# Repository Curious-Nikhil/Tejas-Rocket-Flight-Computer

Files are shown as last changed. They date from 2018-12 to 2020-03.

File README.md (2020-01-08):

# Tejas Flight Computer
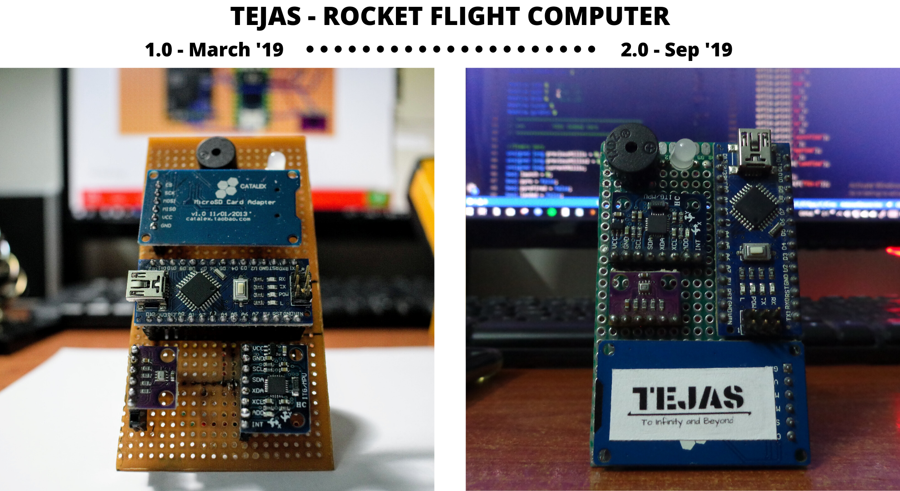
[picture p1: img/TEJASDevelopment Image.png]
TEJAS FC Development

# Software Design

> I prefer to sail in a bad ship with a good captain rather than sail in good ship with a bad captain.

TEJAS flight computer is to aid a model rocket with recovery and data logging. It is entirely based on arduino with MPU6050 and BMP280 for orientation and altitude data. The development of TEJAS FC took over 3 months. It was fundamentally designed with no blocking code so as to make it a fault taularent system to some degree.

## Challenges:
-   
-   Low memory
-   Less Processing Power
-   Delayed Apogge Detection
-   Realtime telemetry

## Flowchart
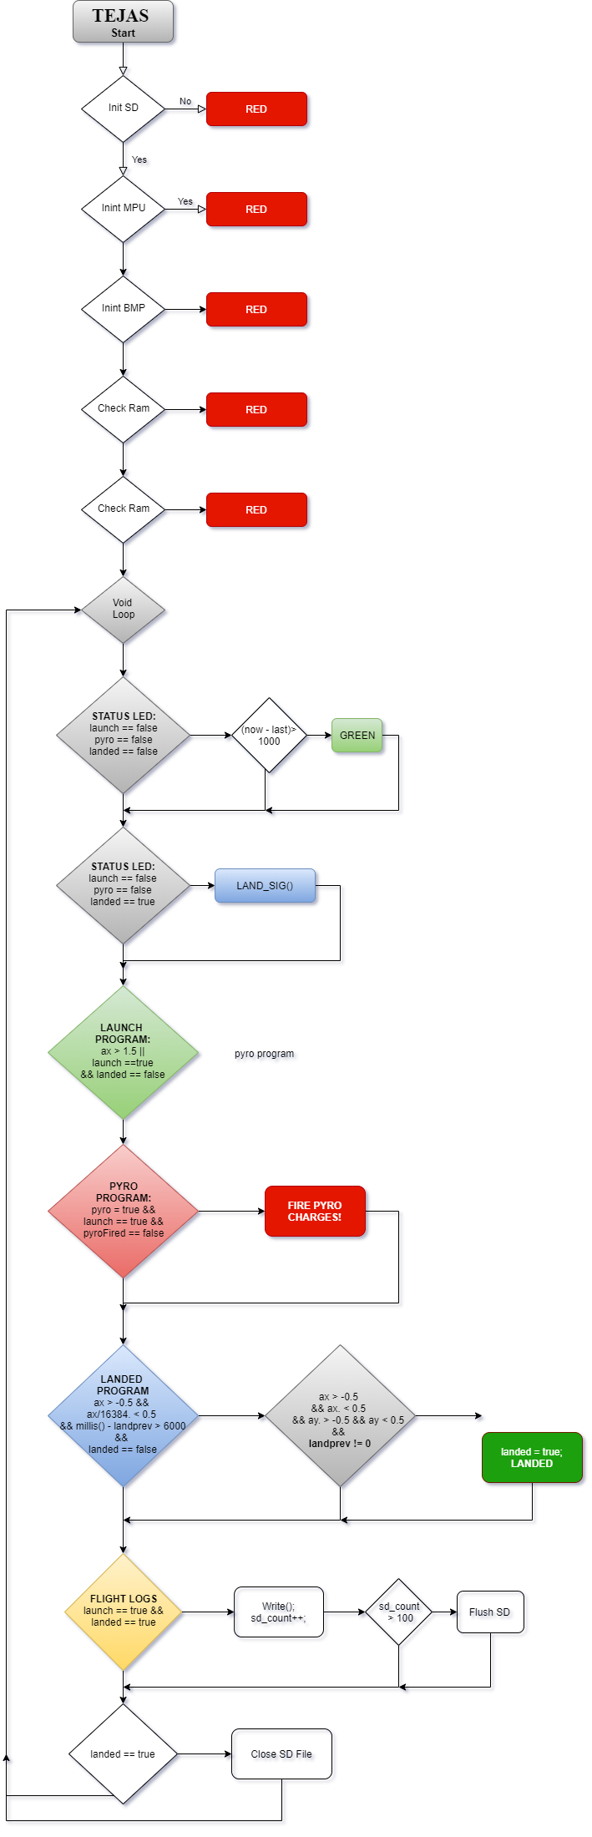
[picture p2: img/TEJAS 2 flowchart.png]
flowchart


### Features of TEJAS 1.0:
-   
-   
-   Systems Check on Boot
-   Non Blocking Code
-   Log Flight Data - Black Box
-   Epic Star Wars Launch sound!

## TEJAS 2.0 A Open Source Rocket Flight Computer. 


### Improvments
 * 1 - Fault Tolerant Soft Design
 * 30 Channel Data logging at 30 Hz
 * BT enabled 
 * Remote Killswitch
 * Better Apogee Detection 
 * Safety Net

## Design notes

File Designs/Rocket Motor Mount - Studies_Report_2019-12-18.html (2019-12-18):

Image Width (pixels):

# Rocket Motor Mount v5 - Stress Study Report

Analyzed File | Rocket Motor Mount v5
Version | Autodesk Fusion 360 (2.0.7036)
Creation Date | 2019-12-18, 11:34:42
Author | Nikhil
Summary | Doing a stress test simulation for a nut bolt rocket motor mount at 20 N thrust.

#### Project Properties

Title | Studies
Author | Nikhil

## Simulation Model 1:1

### Study 2 - Static Stress

##### Study Properties

Study Type | Static Stress
Last Modification Date | 2019-12-18, 11:25:22

#### Settings

##### General

Contact Tolerance | 0.1 mm
Remove Rigid Body Modes | No

##### Mesh

Average Element Size (% of model size)
Solids | 10
Scale Mesh Size Per Part | No
Average Element Size (absolute value) | -
Element Order | Parabolic
Create Curved Mesh Elements | No
Max. Turn Angle on Curves (Deg.) | 60
Max. Adjacent Mesh Size Ratio | 1.5
Max. Aspect Ratio | 10
Minimum Element Size (% of average size) | 20

##### Adaptive Mesh Refinement

Number of Refinement Steps | 0
Results Convergence Tolerance (%) | 20
Portion of Elements to Refine (%) | 10
Results for Baseline Accuracy | Von Mises Stress

#### Materials

Component | Material | Safety Factor
Nut:1 | Plastic, Opaque White | Yield Strength
BoltMount:1/Body1 | Plastic, Opaque White | Yield Strength
BoltMount:1/Body2 | Plastic, Opaque White | Yield Strength

##### Plastic, Opaque White

Density | 9.52E-07 kg / mm^3
Young's Modulus | 911 MPa
Poisson's Ratio | 0.392
Yield Strength | 20.67 MPa
Ultimate Tensile Strength | 13.78 MPa
Thermal Conductivity | 2.11E-04 W / (mm C)
Thermal Expansion Coefficient | 1.5E-04 / C
Specific Heat | 2859 J / (kg C)

#### Contacts

##### Bonded

Name

[S] Bonded1 [BoltMount:1(Body1)||BoltMount:1(Body2)]

[S] Bonded2 [Nut:1||BoltMount:1(Body1)]

#### Mesh

Type | Nodes | Elements
Solids | 45485 | 26022

#### Load Case1

#### Constraints

##### Fixed1

Type | Fixed
Ux | Yes
Uy | Yes
Uz | Yes

###### Selected Entities

For correct interpretation of this image use e.g. IE9, Chrome, Safari, Firefox

#### Loads

##### Force1

Type | Force
Magnitude | 20 N
X Value | 3.175E-14 N
Y Value | 1.086E-13 N
Z Value | -20 N
Force Per Entity | No

###### Selected Entities

For correct interpretation of this image use e.g. IE9, Chrome, Safari, Firefox

#### Results

##### Result Summary

Name | Minimum | Maximum
Safety Factor
Safety Factor (Per Body) | 15 | 15
Stress
Von Mises | 0 MPa | 1.083 MPa
1st Principal | -0.293 MPa | 0.2354 MPa
3rd Principal | -1.229 MPa | 0.07722 MPa
Normal XX | -0.6689 MPa | 0.1515 MPa
Normal YY | -0.8763 MPa | 0.1562 MPa
Normal ZZ | -0.3004 MPa | 0.1657 MPa
Shear XY | -0.04168 MPa | 0.2761 MPa
Shear YZ | -0.2129 MPa | 0.3508 MPa
Shear ZX | -0.2278 MPa | 0.1432 MPa
Displacement
Total | 0 mm | 0.001528 mm
X | -3.513E-04 mm | 3.379E-04 mm
Y | -3.659E-04 mm | 3.373E-04 mm
Z | -0.001527 mm | 2.475E-05 mm
Reaction Force
Total | 0 N | 0.1582 N
X | -0.08786 N | 0.09729 N
Y | -0.07294 N | 0.1013 N
Z | -0.05085 N | 0.1135 N
Strain
Equivalent | 0 | 0.001897
1st Principal | -2.916E-06 | 0.001177
3rd Principal | -0.001966 | 0
Normal XX | -2.928E-04 | 6.555E-05
Normal YY | -6.097E-04 | 6.938E-05
Normal ZZ | -7.374E-05 | 5.149E-04
Shear XY | -1.274E-04 | 8.438E-04
Shear YZ | -6.506E-04 | 0.001072
Shear ZX | -6.963E-04 | 4.375E-04
Contact Pressure
Total | 0 MPa | 0.5267 MPa
X | -0.2684 MPa | 0.1044 MPa
Y | -0.1016 MPa | 0.3981 MPa
Z | -0.261 MPa | 0.0706 MPa

##### Safety Factor

###### Safety Factor (Per Body)

0 8

For correct interpretation of this image use e.g. IE9, Chrome, Safari, Firefox

##### Stress

###### Von Mises

[MPa] 0 1.083

For correct interpretation of this image use e.g. IE9, Chrome, Safari, Firefox

###### 1st Principal

[MPa] -0.293 0.2354

For correct interpretation of this image use e.g. IE9, Chrome, Safari, Firefox

###### 3rd Principal

[MPa] -1.229 0.077

For correct interpretation of this image use e.g. IE9, Chrome, Safari, Firefox

##### Displacement

###### Total

[mm] 0 0.001528

For correct interpretation of this image use e.g. IE9, Chrome, Safari, Firefox

Image Width (pixels):

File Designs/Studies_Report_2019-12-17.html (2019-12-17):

Image Width (pixels):

# Study Report

Analyzed File | BlastCoupler v1
Version | Autodesk Fusion 360 (2.0.7036)
Creation Date | 2019-12-17, 22:31:43
Author | Nikhil

#### Project Properties

Title | Studies
Author | Nikhil

## Simulation Model 1:1

### Study 2 - Thermal

##### Study Properties

Study Type | Thermal
Last Modification Date | 2019-12-17, 22:20:57

#### Settings

##### General

Contact Tolerance | 0.1 mm
Global Initial Temperature | 20 C

##### Mesh

Average Element Size (% of model size)
Solids | 10
Scale Mesh Size Per Part | No
Average Element Size (absolute value) | -
Element Order | Parabolic
Create Curved Mesh Elements | No
Max. Turn Angle on Curves (Deg.) | 60
Max. Adjacent Mesh Size Ratio | 1.5
Max. Aspect Ratio | 10
Minimum Element Size (% of average size) | 20

##### Adaptive Mesh Refinement

Number of Refinement Steps | 0
Results Convergence Tolerance (%) | 20
Portion of Elements to Refine (%) | 10
Results for Baseline Accuracy | Heat Flux

#### Materials

Component | Material | Safety Factor
Body1 | Plastic, Opaque White | Yield Strength

##### Plastic, Opaque White

Density | 9.52E-07 kg / mm^3
Young's Modulus | 911 MPa
Poisson's Ratio | 0.392
Yield Strength | 20.67 MPa
Ultimate Tensile Strength | 13.78 MPa
Thermal Conductivity | 2.11E-04 W / (mm C)
Thermal Expansion Coefficient | 1.5E-04 / C
Specific Heat | 2859 J / (kg C)

#### Contacts

#### Mesh

Type | Nodes | Elements
Solids | 3743 | 2216

#### Load Case1

#### Loads

##### Applied Temperature1

Type | Applied Temperature
Value | 200 C

###### Selected Entities

For correct interpretation of this image use e.g. IE9, Chrome, Safari, Firefox

##### Convection1

Type | Convection
Convection Value | 5 W / (m^2 K)
Ambient Temperature | 25 C

###### Selected Entities

For correct interpretation of this image use e.g. IE9, Chrome, Safari, Firefox

#### Results

##### Result Summary

Name | Minimum | Maximum
Temperature
Temperature | 139.7 C | 200 C
Heat Flux
Total | 6.791E-04 W / mm^2 | 0.002224 W / mm^2
X | -7.419E-04 W / mm^2 | 7.508E-04 W / mm^2
Y | -7.469E-04 W / mm^2 | 7.547E-04 W / mm^2
Z | 6.116E-04 W / mm^2 | 0.002148 W / mm^2
Thermal Gradient
Total | 3.218 C / mm | 10.54 C / mm
X | -3.558 C / mm | 3.516 C / mm
Y | -3.577 C / mm | 3.54 C / mm
Z | -10.18 C / mm | -2.899 C / mm
Applied Heat Flow
Applied Heat Flow | -1.618E-20 W / mm^2 | 9.367E-10 W / mm^2

##### Temperature

###### Temperature

[C] 139.7 200

For correct interpretation of this image use e.g. IE9, Chrome, Safari, Firefox

Image Width (pixels):

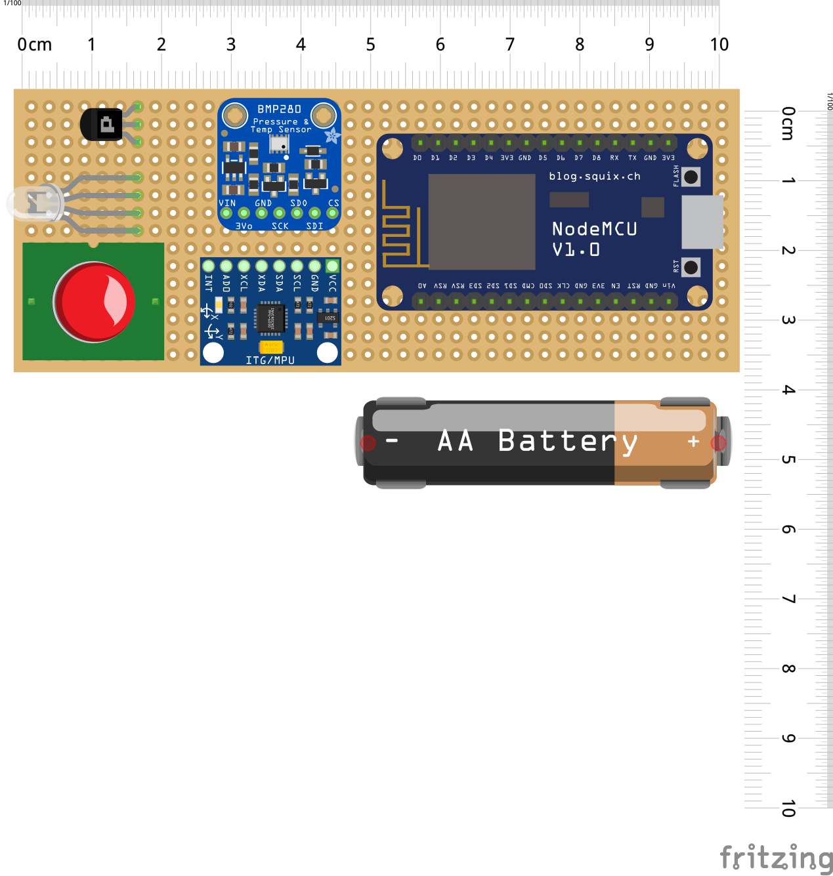
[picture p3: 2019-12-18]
Designs/PCB/TEJAS 2_PCB_bb.png

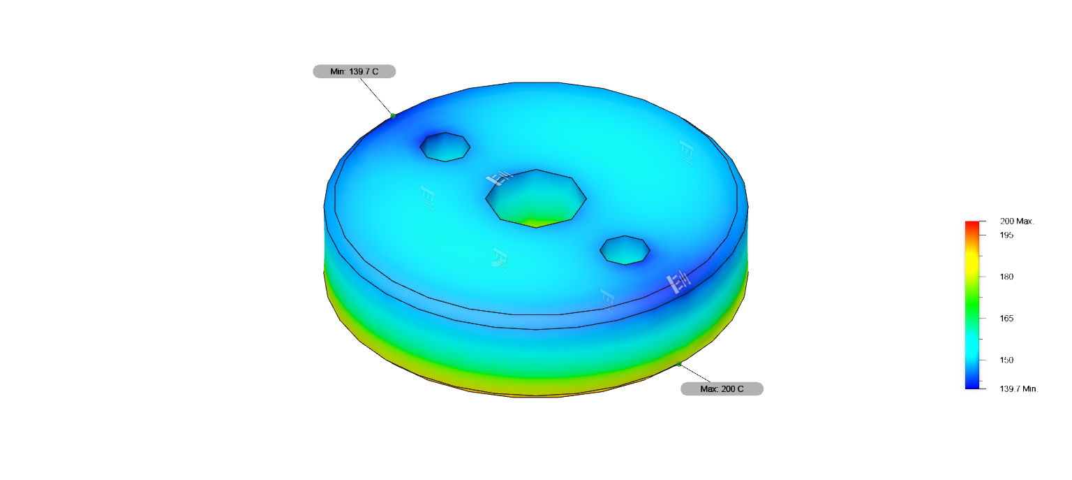
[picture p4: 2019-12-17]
Designs/BlastCoupler v4.png

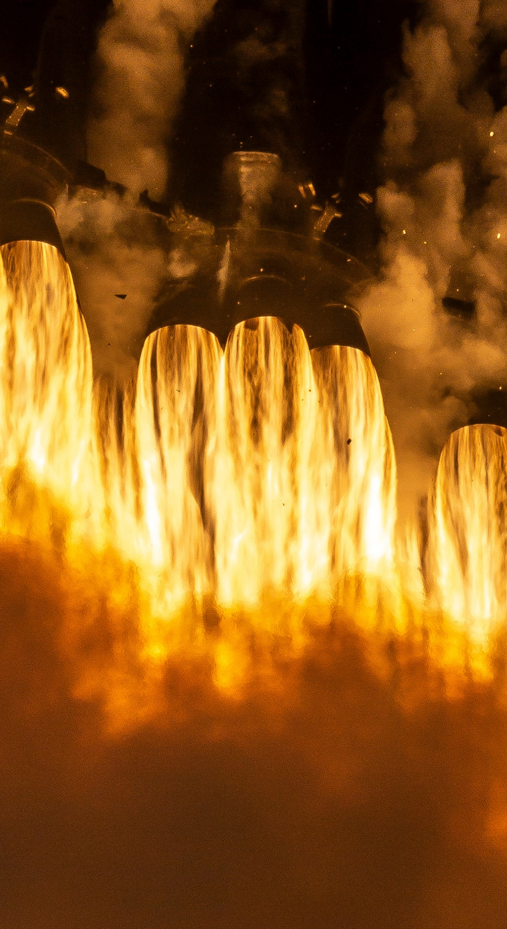
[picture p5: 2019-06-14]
Tejas Android App/Untitled design.jpg

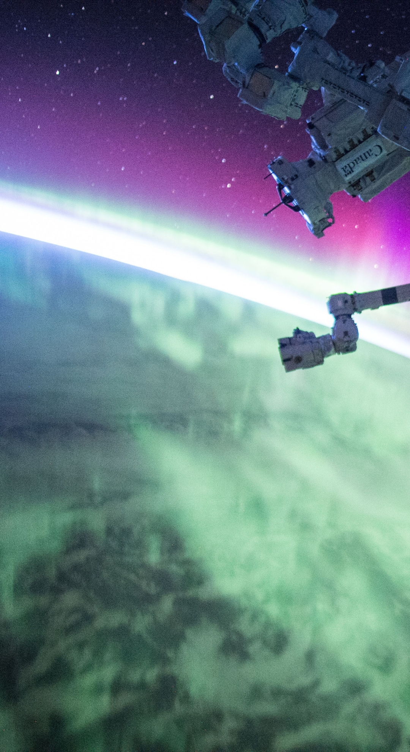
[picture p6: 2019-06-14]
Tejas Android App/Untitled design (1).jpg

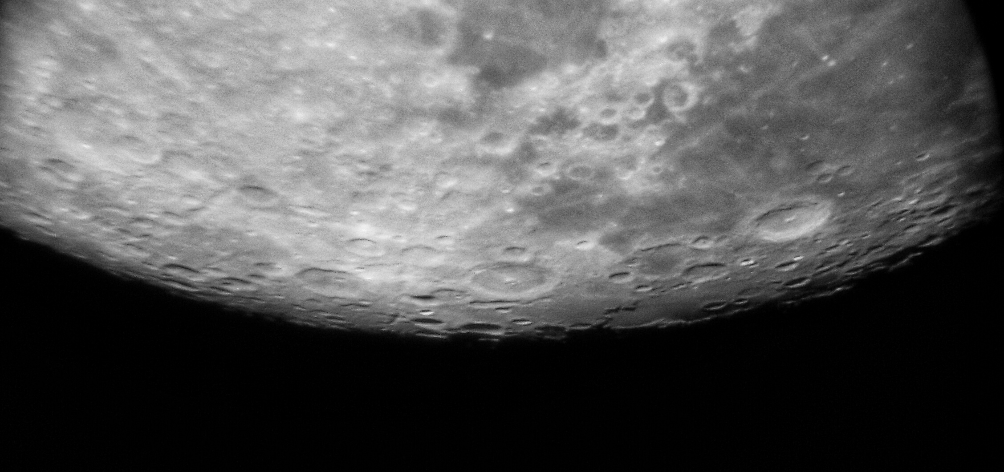
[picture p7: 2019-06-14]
Tejas Android App/29610276573_0eec8b728a_o.jpg

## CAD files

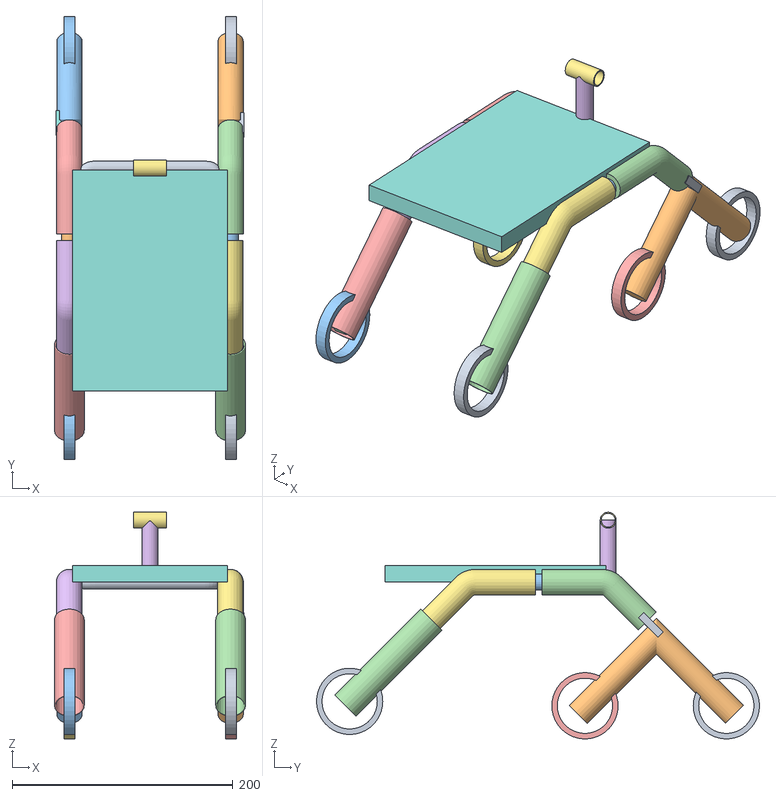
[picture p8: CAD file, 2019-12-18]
Designs/Rover V1 v12.obj
173.0 x 401.0 x 205.2
Solar Panel

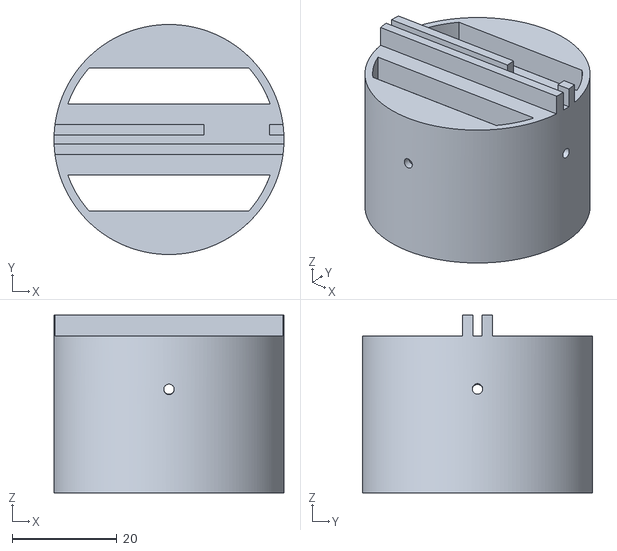
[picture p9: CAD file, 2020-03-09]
Designs/Tejas - Parts/Flight Computer Mount/FC_Upper_Mount_V10.stl
44.0 x 44.0 x 34.0

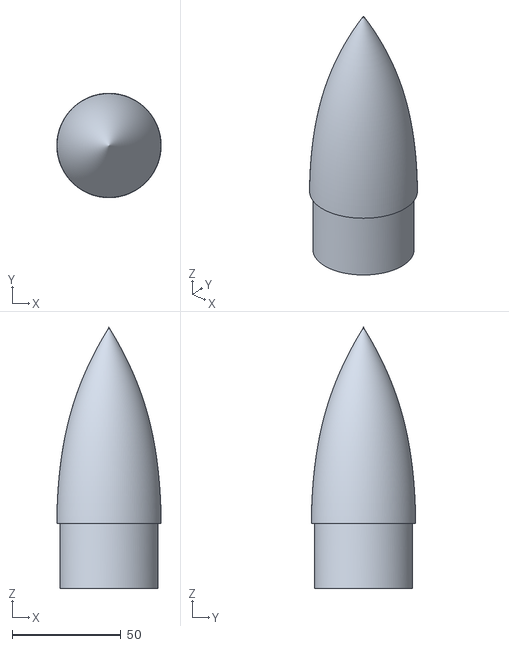
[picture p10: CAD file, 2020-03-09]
Designs/Tejas - Parts/Rocket Nose Cone v13.stl
48.0 x 48.0 x 120.0

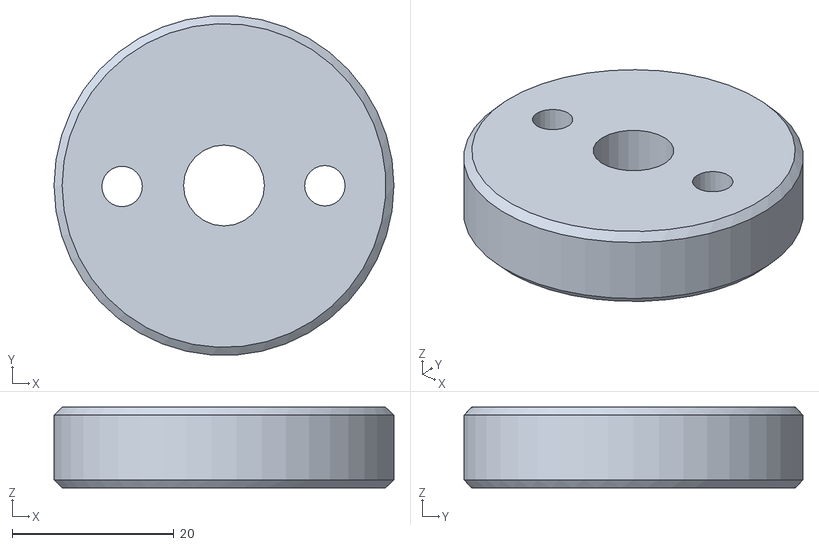
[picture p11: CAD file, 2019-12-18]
Designs/BlastCoupler v1.obj
42.0 x 41.9 x 10.0

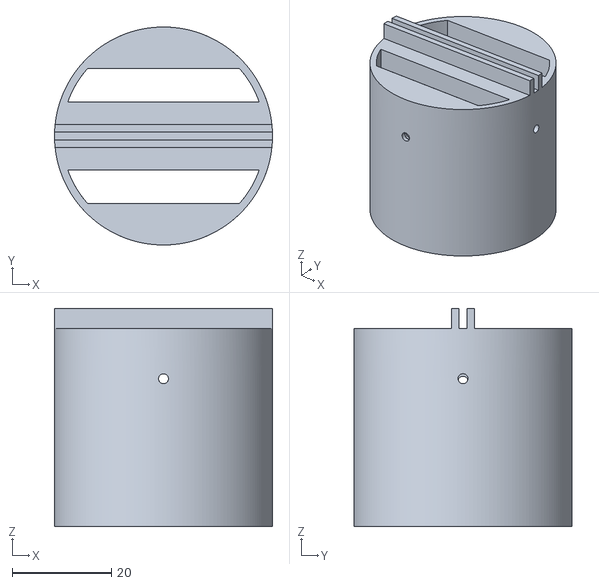
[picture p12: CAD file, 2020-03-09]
Designs/Tejas - Parts/Flight Computer Mount/FC_Lower_Mount_V10.stl
44.0 x 44.0 x 44.0

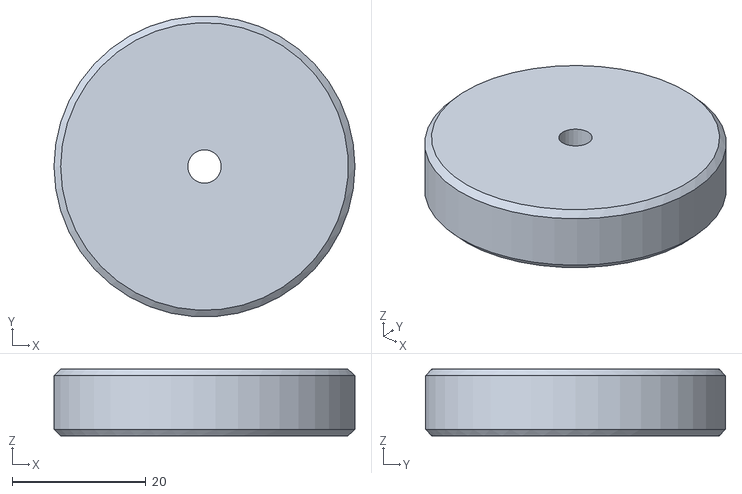
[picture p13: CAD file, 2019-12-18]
Designs/Coupler1 v4.obj
45.0 x 44.9 x 10.0

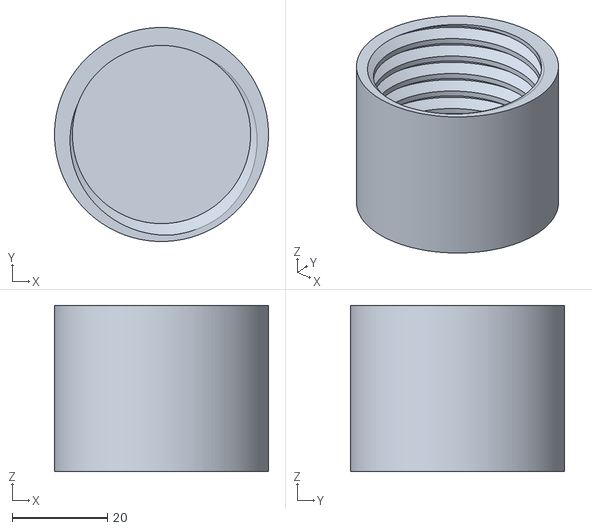
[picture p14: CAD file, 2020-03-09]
Designs/Tejas - Parts/Motor Mount/MotorMount - Nut V12.stl
45.0 x 45.0 x 35.0

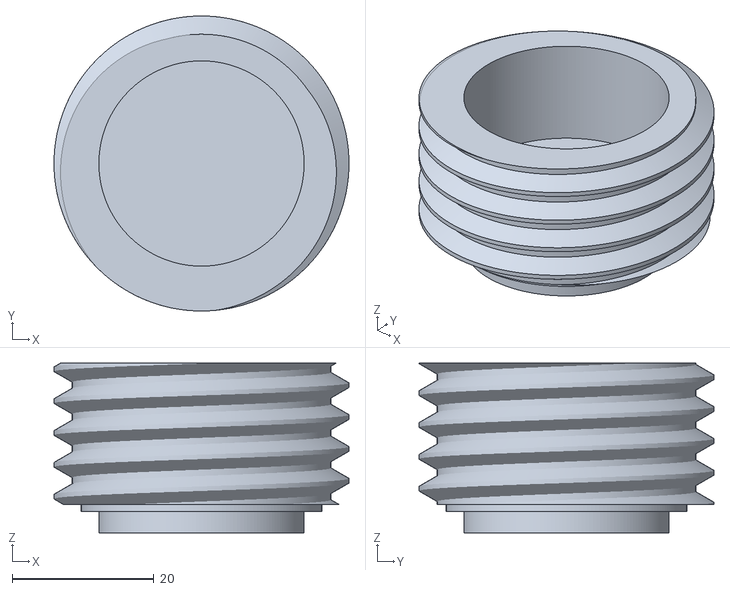
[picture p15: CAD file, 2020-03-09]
Designs/Tejas - Parts/Motor Mount/MotorMount - Bolt V12.stl
41.7 x 41.7 x 24.0

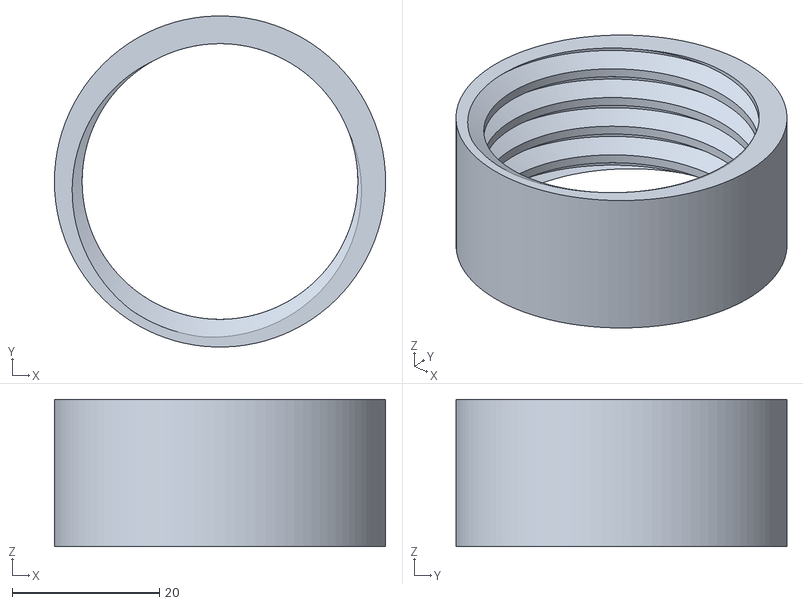
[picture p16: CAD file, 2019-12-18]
Designs/MotorMount - Nut.stl
45.0 x 45.0 x 20.0

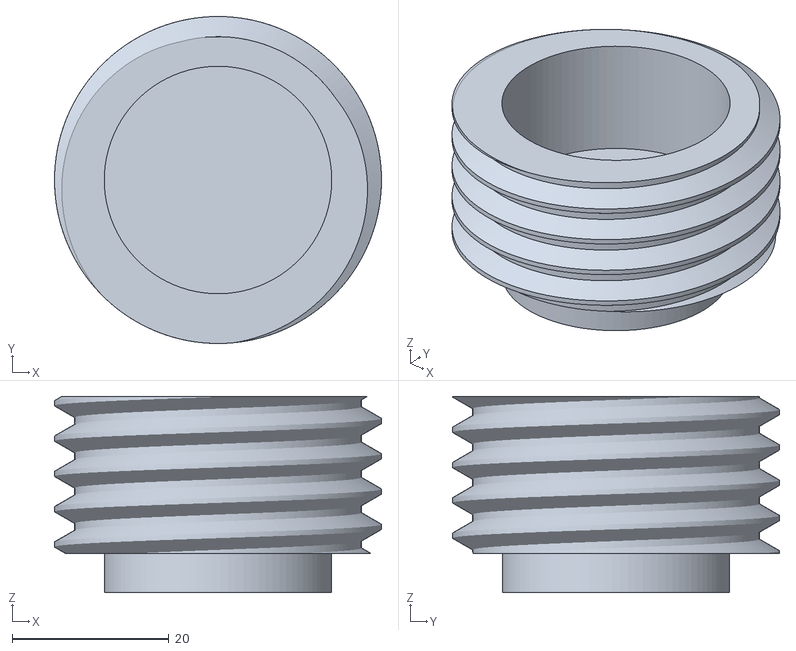
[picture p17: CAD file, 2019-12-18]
Designs/MotorMount - Bolt.stl
41.7 x 41.7 x 25.0

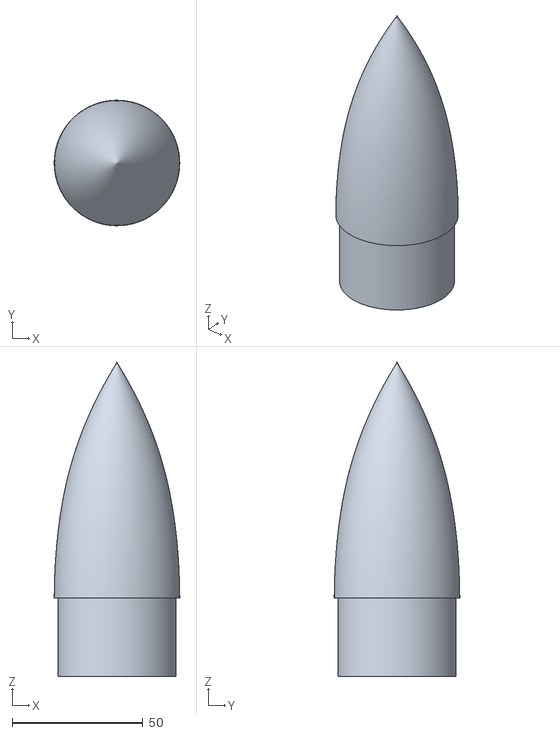
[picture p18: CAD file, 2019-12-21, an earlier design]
Designs/Tejas - Parts/Rocket Nose Cone v12.stl
48.0 x 48.0 x 120.0

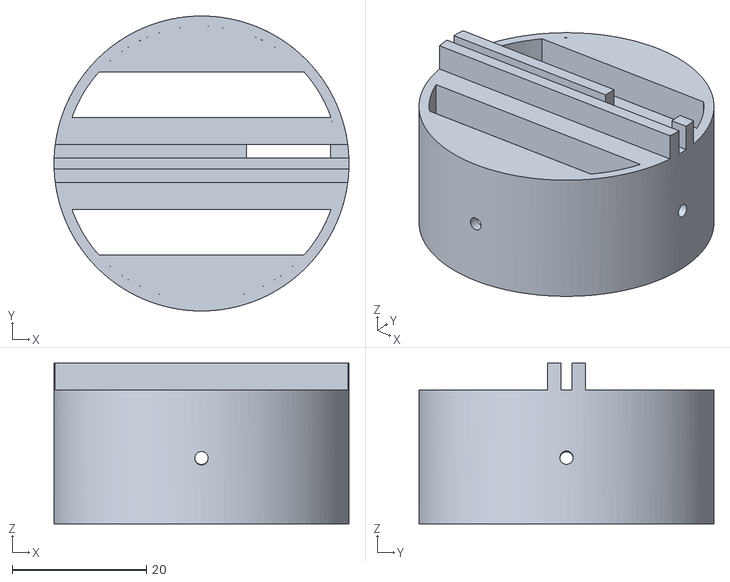
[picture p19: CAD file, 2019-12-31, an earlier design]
Designs/Tejas - Parts/Flight Computer Mount/FC_Upper_Mount_V8.stl
44.0 x 44.0 x 24.0

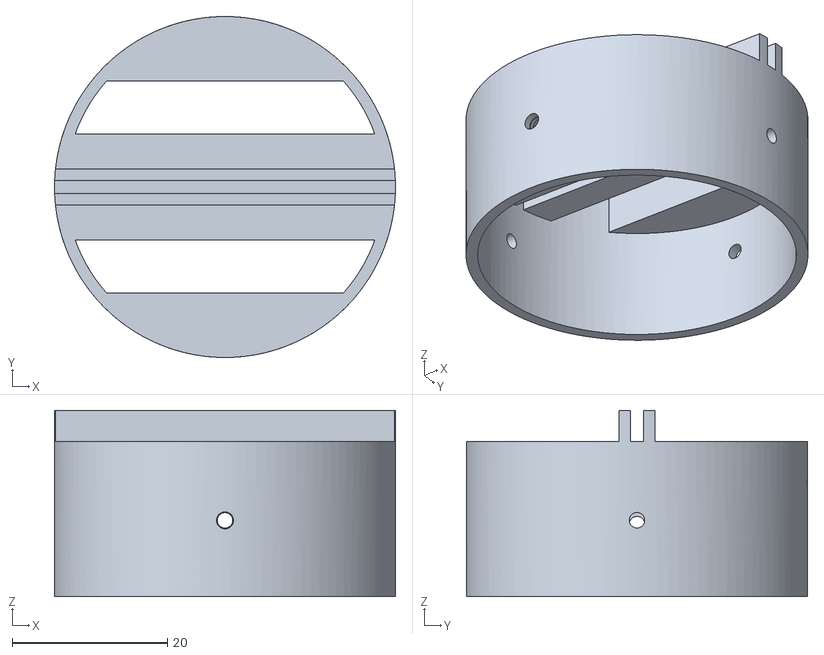
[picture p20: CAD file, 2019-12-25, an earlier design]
Designs/Tejas - Parts/Flight Computer Mount/FC_Lower_Mount_V8.stl
44.0 x 44.0 x 24.0

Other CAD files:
Designs/Tejas - Parts/BlastCoupler v2.stl
Designs/Tejas - Parts/Coupler1 v4.stl
Designs/Coupler1 v3.stl
Designs/Rocket Nose Cone v7.stl
Designs/Tejas - Parts/Rocket Nose Cone v7.stl
Designs/Rocket Nose Cone v2.stl
Designs/Rocket Nose Cone v7.obj
Designs/TVC Mount/TVC_0/Rocket Model.skp
Designs/Tejas - Parts/Flight Computer Mount/FC_Lower_Mount_V6.stl
Designs/Tejas - Parts/Flight Computer Mount/FC_Upper_Mount_V6.stl
Designs/Tejas - Parts/Motor Mount/MotorMount - Bolt V2.stl
Designs/Tejas - Parts/Motor Mount/MotorMount - Nut V2.stl

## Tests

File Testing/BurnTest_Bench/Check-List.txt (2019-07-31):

start

check for main activation switch

check for button state
    Use Interrupts

enable button

check continuity

ignite

start reading data

 * close loadcell
 * close file

--------------
add bluetooth support

50

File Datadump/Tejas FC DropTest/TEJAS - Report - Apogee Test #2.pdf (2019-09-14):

# Flight Computer Apogee Test #2

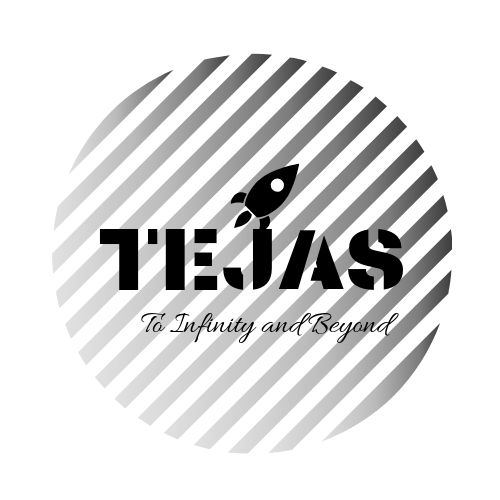
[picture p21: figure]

The Tejas Flight Computer is designed to detect various phases of flight and act accordingly. It has an accelerometer, gyroscope and a barometer for orientation and altitude data.

The Flight Computer was thrown in a parabolic trajectory to simulate the conditions during powered
flight.

The sensors didn’t perform well because the

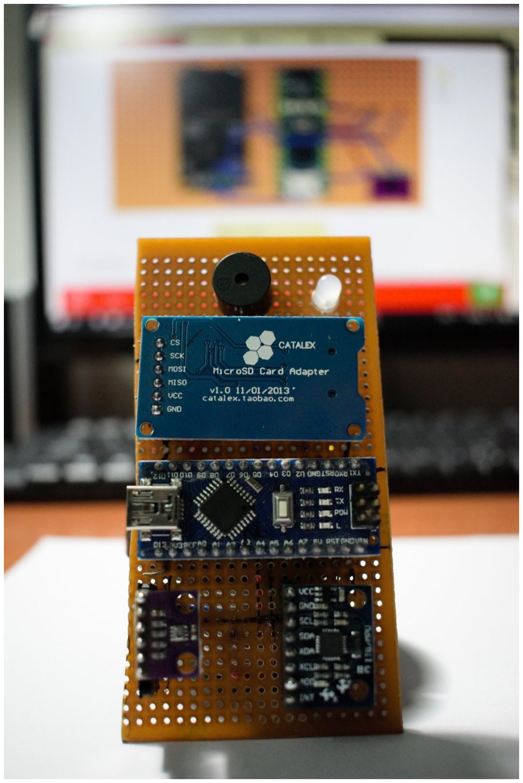
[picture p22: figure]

Avionics Bay has no opening to allow for the sensor | to
perceive actual pressure change.

## High Altitude Drop Test:

A high altitude drop test is necessary to test the integrity of the system if the rocket were to experience a terminal velocity crash. The test showed that the female header pins were the weakest part of the system. Also, the crash force destroyed the Arduino because of its contact with the inner wall of the Avionics Bay.

Some sort of cushioning could help the TEJAS flight computer survive the fall.

Here’s the data:

TEJAS Test Reports
Date: 24 Aug 2019

## Reason for Inconclusive Data:

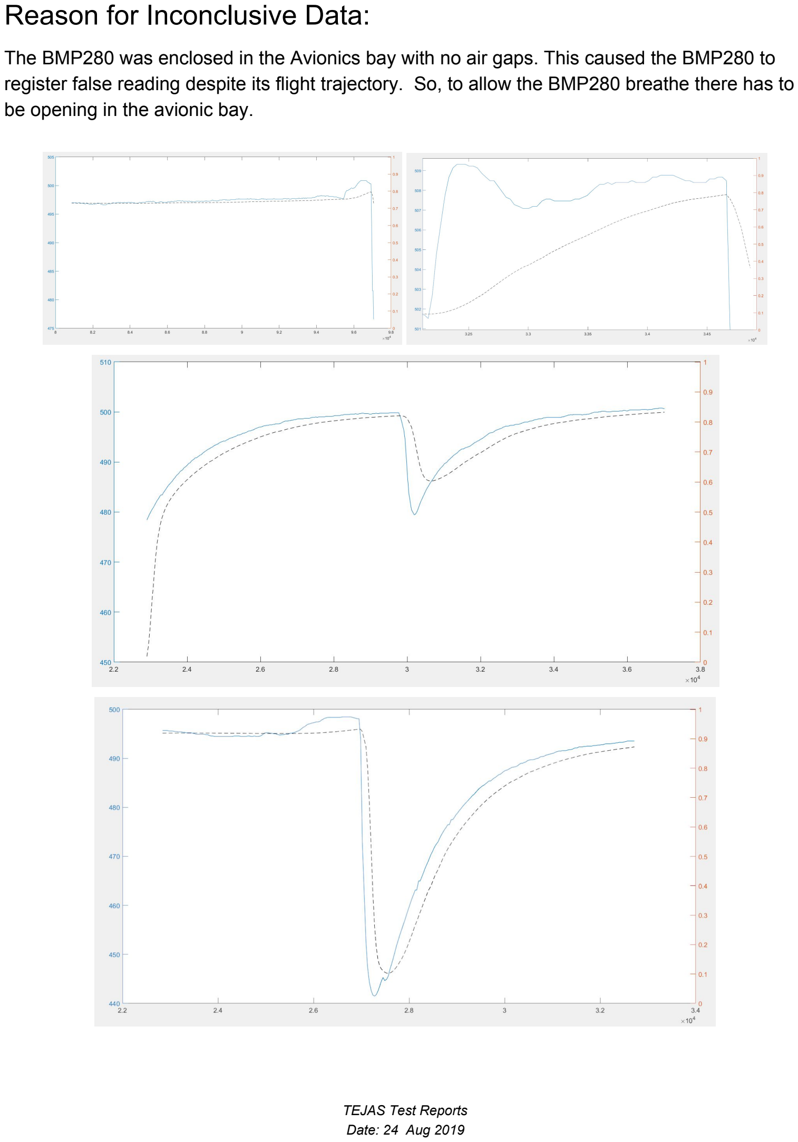
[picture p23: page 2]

The BMP280 was enclosed in the Avionics bay with no air gaps. This caused the BMP280 to register false reading despite its flight trajectory. So, to allow the BMP280 breathe there has to be opening in the avionic bay.

More Pics:

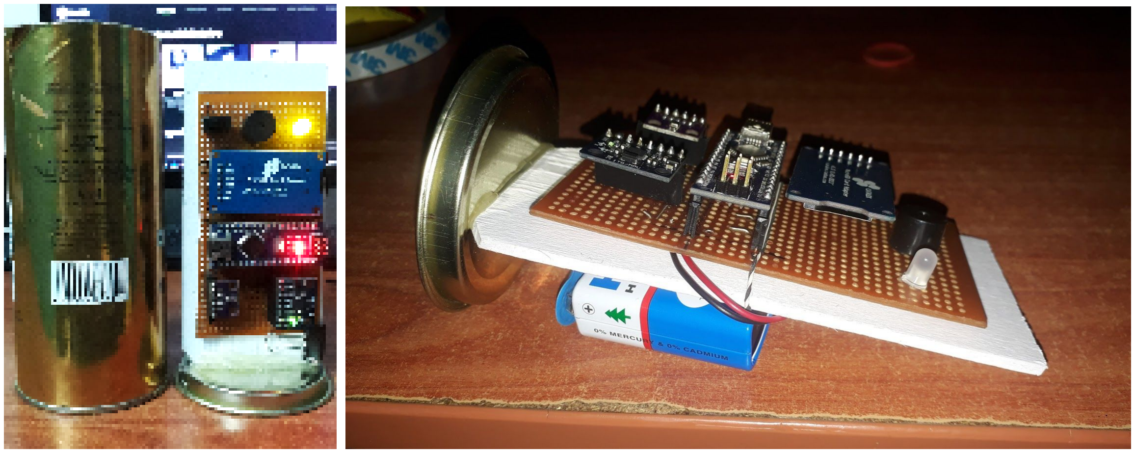
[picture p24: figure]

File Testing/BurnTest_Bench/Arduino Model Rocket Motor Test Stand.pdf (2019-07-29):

## Arduino Model Rocket Motor Test Stand

## Nick Cinquino and Len Johnson, 10/2015

Combining an Arduino Uno microcontroller, an LCD keypad shield, an HX711 breakout board, a 10Kg loadcell, and a custom made engine mount yields a sensitive and accurate test stand or dynamometer for testing the thrust in Newtons of model rocket motors. The circuit is also usable as a stand-alone gram scale.

Functionally, a model rocket motor is affixed to a loadcell, which generates a very small analog voltage difference, proportional to the force applied. The small voltage is applied to an HX711 breakout board, which amplifies the voltage and converts to serial digital data. The serial data is received by the Arduino microcontroller, which applies a calibration factor so that output is shown as grams of force. When a motor is affixed to the loadcell, and the igniter is placed and wired, AND the momentary pushbutton is activated, a 10-second warning time begins, with flashing of a bright yellow LED. When the 10 seconds is up, the yellow LED turns off, a red LED turns on, and a relay is closed allowing the full 12V from a gel-cell battery to be applied to the igniter. Immediately afterwards, the Arduino logs the time, and begins acquiring force data at 80 samples per second. After 800 readings are acquired, the relay shuts down, acquisition stops and the stop time is logged. In the meantime, the Arduino is also displaying gram-force on the LCD display, and showing the status of the acquisition run.

Beginning with the loadcell, they are a beam with strain gages attached, in a Wheatstone Bridge arrangement. Loadcells can be purchased new from several sources including Sparkfun, or Aliexpress.com, or may be liberated from old, nonfunctional industrial scales.
Fig.1 shows a collection of loadcells from old scales…the electronics break down long before the loadcell does! The large one at center is rated to 2400Lb!

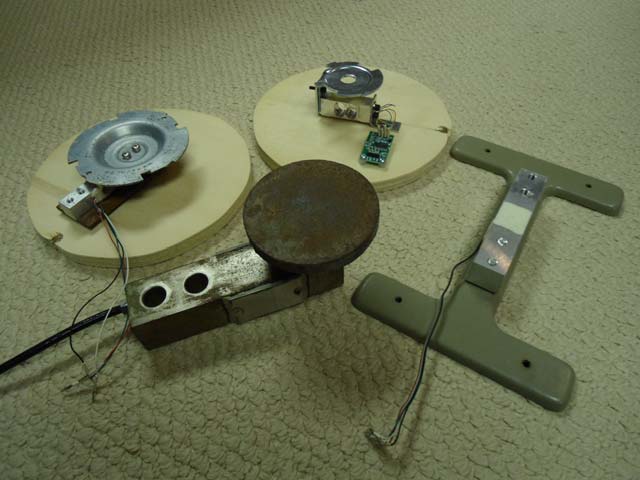
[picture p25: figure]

Fig.1

Next is the HX711 breakout board. The one in use is the YL-112 module from Aliexpress.com. The cable between the HX711 board and Arduino should be at least 4’. One easy hack is necessary: to change the sample rate from 10 samples per second to 80 samples per second, pin 15 needs to be desoldered from ground, and attached to +5 instead. This is done by using a fine tipped iron, and using a needle to pull up the pin the instant the solder melts. After the pin is bent up, run a short jumper from the pin to any +5V spot on the board. An even easier option is to use the Sparkfun HX711 board which is configurable for either 10 or 80 sa/sec. Fig.2 shows the HX711 hack:

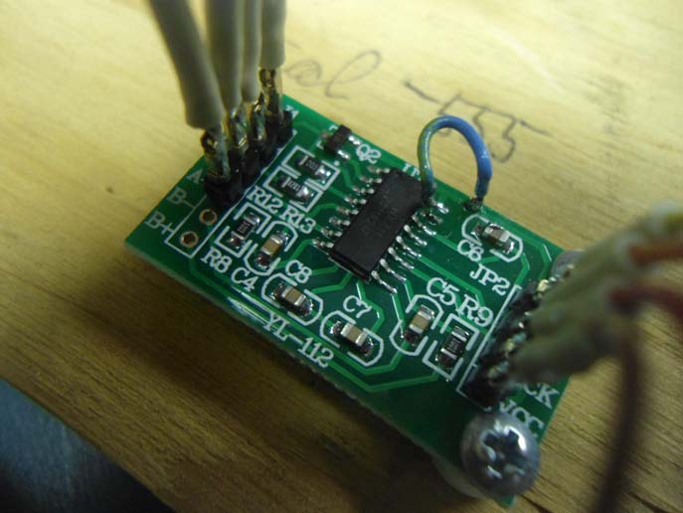
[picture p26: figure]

Fig.2: Desolder pin 15 from ground, jumper to +5V.

Arduino Uno/LCD Keypad shield: solder headers to the top row of the LCD shield and to the bottom 2 rows. Pin identifications on the top row of the shield, from left to right are D13, D12, D11, D3, D2, D1, D0 to the Arduino. Plug the LCD shield into the Arduino and add the remainder of the circuit except for the 12V/igniter section, fig.3:

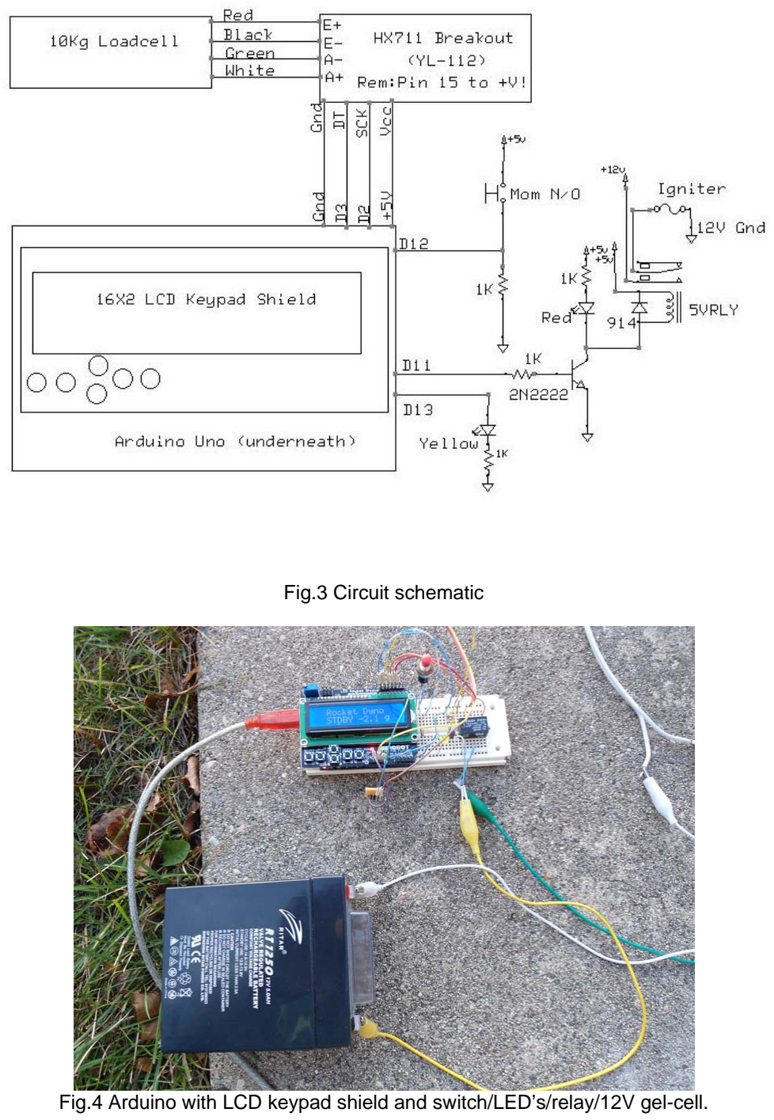
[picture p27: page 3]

Fig.3 Circuit schematic

Fig.4 Arduino with LCD keypad shield and switch/LED’s/relay/12V gel-cell.

Programming/Sketch: The HX711 library is needed; download from Github (see references) and add to your library folder. Then copy/paste the following sketch into your Arduino IDE window:

/*
Model Rocket Engine Dynamometer - Nick Cinquino 9/1/15 - V.5 Original 10Kg loadcell Modified from Nathan Seidle, SparkFun Electronics, November 19th, 2014
Output data in grams (g). There are 101.97 gram-force per Newton, for conversion. Your calibration factor may be very positive or very negative. It all depends on the setup of your individual loadcell, and the direction the sensors deflect from zero state. Need to experiment!
Hack the HX711 board to set pin 15 high, for 80 samples per second.
This example code uses bogde's excellent library: https://github.com/bogde/HX711 bogde's library is released under a GNU GENERAL PUBLIC LICENSE
Arduino pin 2 - HX711 Clock
pin 3 - Serial Data In
5V - VCC
GND - GND
Yellow LED on pin 13, igniter transistor/relay on pin 11, momentary pushbutton on pin 12.
Most any pin on the Arduino Uno will be compatible with DOUT/CLK.
The HX711 board can be powered from 2.7V to 5V so the Arduino 5V power is fine.

*/

#include "HX711.h"

#include <LiquidCrystal.h>

LiquidCrystal lcd(8,9,4,5,6,7);
const int buttonPin = 12; | // start sequence button
const int ledPin = 13; | //LED indicator and/or buzzer
const int igniterPin = 11; //igniter transistor circuit
int buttonState = 0;
#define DOUT 3

#define CLK 2

HX711 scale(DOUT, CLK);
float calibration_factor = -560; //-560 works for my 10kg loadcell.

void setup() {
pinMode(buttonPin, INPUT);
pinMode(igniterPin, OUTPUT);
pinMode(ledPin, OUTPUT);
Serial.begin(9600);
Serial.println("HX711 Rocket Motor Dynamometer, V.5"); Serial.println("Affix motor nozzle up. Place igniter in nozzle. Move away from test stand.");
Serial.println("Press start button to initialize ignition sequence.");
lcd.begin(16, 2);
lcd.clear();

lcd.setCursor(0,0);
lcd.print(" MODEL ROCKET"); lcd.setCursor(0,1);
lcd.print(" DYNAMOMETER"); delay(2000);
scale.set_scale();
scale.tare(); //Reset the scale to 0
long zero_factor = scale.read_average(); //Get a baseline reading Serial.print("Zero factor: "); //This can be used to remove the need to tare the scale. Useful in permanent scale projects.
Serial.println(zero_factor);
Serial.println(" ");
}

void loop() {
lcd.clear();
lcd.setCursor(0,0);
lcd.print(" Rocket Dyno"); lcd.setCursor(0,1);
lcd.print(" STDBY " );
scale.set_scale(calibration_factor); lcd.print(scale.get_units(),1); lcd.print(" g");
delay(500);
buttonState = digitalRead(buttonPin); if (buttonState == HIGH) {

lcd.clear();
lcd.setCursor(0,0);
lcd.print(" Rocket Dyno");
lcd.setCursor(0,1);
lcd.print(" STAND CLEAR!"); Serial.println("IGNITION SEQUENCE ACTIVATED!");

for (int i=0; i <= 50; i++){
digitalWrite(ledPin, HIGH);
delay (100);
digitalWrite (ledPin,LOW); delay (100);
}
lcd.clear();
lcd.setCursor(0,0);
lcd.print(" Rocket Dyno"); lcd.setCursor(1,1);
lcd.print(" AQUIRING DATA"); digitalWrite(igniterPin, HIGH); Serial.print("Start time, ms: "); Serial.print (millis());
Serial.println(" ");
Serial.println();

for (int i=0; i <= 800; i++){ //800 samples at 80sa/sec = 10 seconds theoretical scale.set_scale(calibration_factor); //Adjust to the calibration factor Serial.print(scale.get_units(), 1);
Serial.println();
}
Serial.println();
Serial.print("Stop Time, ms: "); Serial.print(millis());
digitalWrite (ledPin,LOW); digitalWrite (igniterPin,LOW); Serial.println();
}
}

Note the line highlighted in yellow: this is the calibration factor that the Arduino uses to convert the signal from the loadcell/HX711 into grams. This value varies widely, even for 2 apparently identical loadcells! You just have to place a known weight in grams on the loadcell and try some values until you zero in on the best value that reads your calibration weight in grams on the LCD.

Loadcell/motor mount: This can be designed and built to suit; the general guidelines are, keep it light (no use in burning up dynamic range), and, importantly, nonflammable! Ours uses a thin sheet steel circular base (such as the cutout from a coffee can) bolted down to the loadcell, with a cemented motor tube with retaining clip attached to the center of the steel base. The motor tube is a half inch longer than the motor, with vent holes at the bottom so that on ejection, the motor moves forward against the retaining clip while ejection gases escape via the bottom vents. Fig.5 shows the loadcell with base:

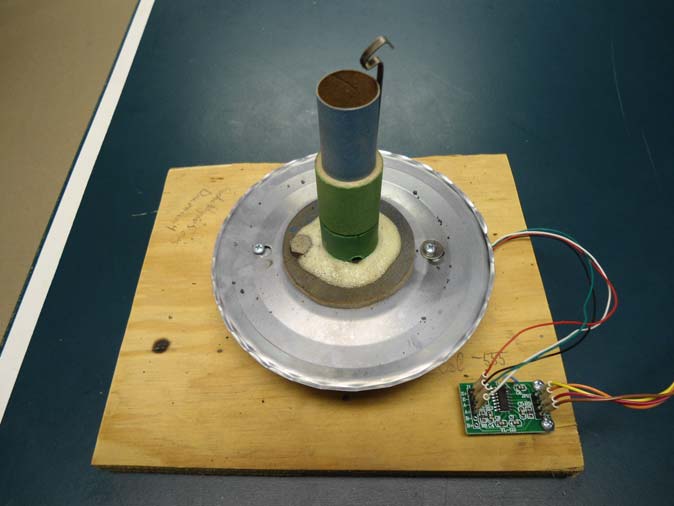
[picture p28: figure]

Fig.5 Motor mount on loadcell

When all systems are ready and connected and the Arduino is running the program, open the Arduino serial window on your laptop. Observe the LCD information. Push the momentary pushbutton. The yellow LED should start blinking, for 10 seconds. Then the red LED turns on and you should hear the relay click. Data should start streaming rapidly on the screen, and stop after 10 seconds. Relay clicks off. Take note of the start time and stop time on-screen. Subtract stop from start time to get delta T. Divide by 800 to get milliseconds per sample (should be around 11), useful for the chart X axis. Convert to samples per second (1/X) which should be between 80-90sa/sec. Copy only the weight data column, and paste into Excel. Make a line chart of this test run.

If everything above went well, you’re ready for a burn test! Make sure the area all around is free of anything flammable. Set up your laptop, with a 6’ USB cable to the Arduino section, then the 4’ cable to the HX711/loadcell section. Leave the 12V battery unconnected until the last step. Open the Arduino serial window. Check status. Insert motor into your loadcell/motor mount, and add igniter. Connect igniter to igniter leads (battery is still unconnected). Move back to the Arduino section, check status on LCD and LED’s. If everything is go, then connect the 12V battery, and push the momentary button, move away from the area.

When the run completes, as in the test, note the start and stop times and copy/paste the gram data into Excel. If desired, add a new column converted into Newtons (grams / 101.97 = Newtons). Generate an exact time scale from the stop – start calculation. Following are results from 2 runs of (old) C6-5 motors:

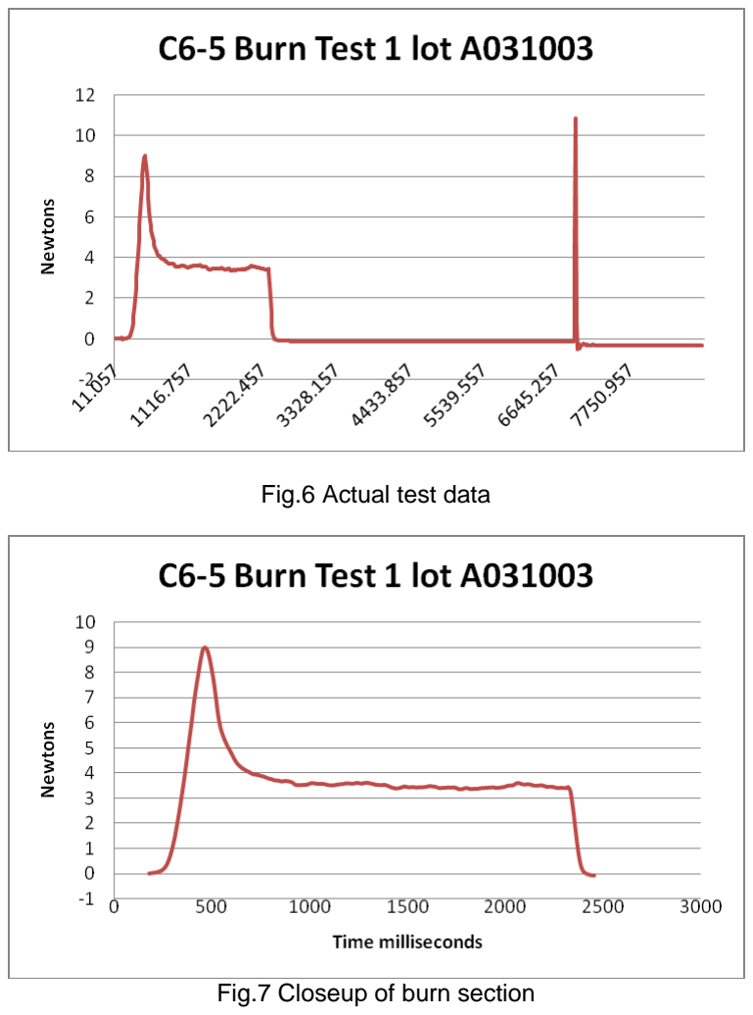
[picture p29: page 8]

Fig.6 Actual test data

Fig.7 Closeup of burn section

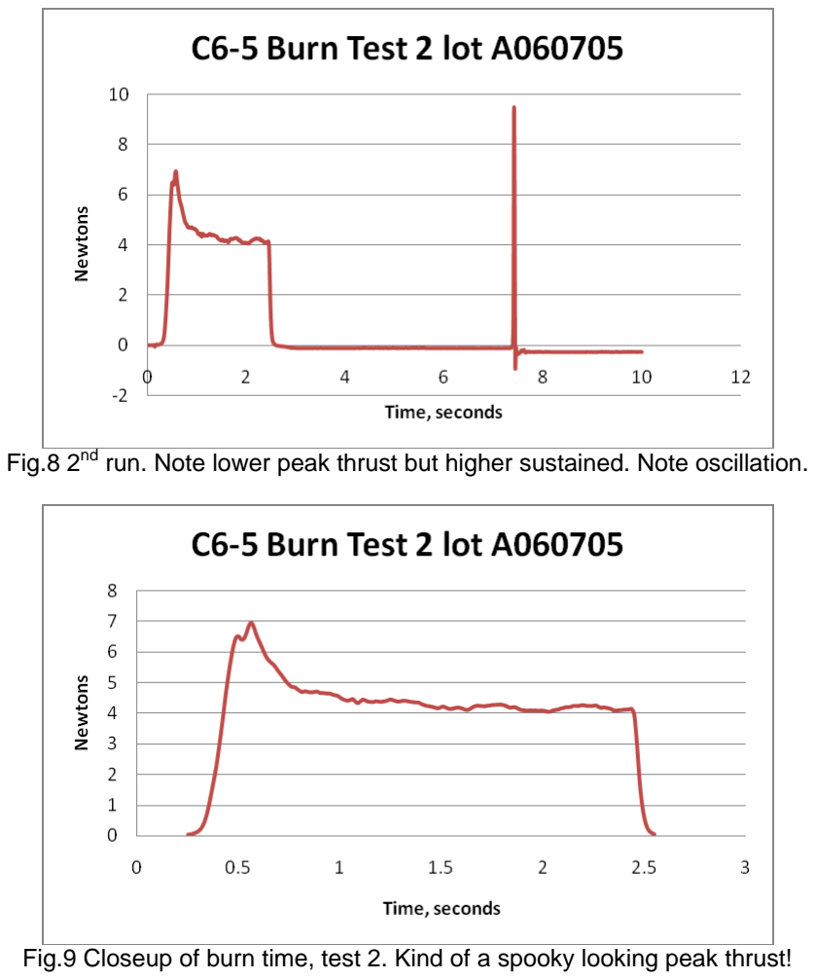
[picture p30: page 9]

Fig.8 2nd run. Note lower peak thrust but higher sustained. Note oscillation.

Fig.9 Closeup of burn time, test 2. Kind of a spooky looking peak thrust!


Fig.10 Anticipated thrust curve of a C6 motor; higher than what we found from old motors.
Note that the test motors burned slightly longer.

References:
Github source of HX711 library:
https://github.com/bogde/HX711

HX711 board:
https://learn.sparkfun.com/tutorials/load-cell-amplifier-hx711-breakout-hookup-guidehttp://www.aliexpress.com/item/For-Arduino-Dual-channel-HX711-Weighing-Pressure-S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

Loadcell sources:
www.aliexpress.com/ (search loadcell on the site)
https://www.sparkfun.com/products/13329

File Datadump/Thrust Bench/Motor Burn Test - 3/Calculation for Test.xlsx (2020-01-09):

 | Time | Weight | time diff
100041 | 7.239 | 9.6 | 0.095
100136 | 7.334 | 12.3 | 0.095
100233 | 7.431 | 46.4 | 0.097
100328 | 7.526 | 273.6 | 0.095
100423 | 7.621 | 2349.2 | 0.095
100519 | 7.717 | 2477.9 | 0.096
100615 | 7.813 | 138.5 | 0.096
100710 | 7.908 | 198.5 | 0.095
100810 | 8.008 | 113.8 | 0.1
100901 | 8.099 | 105 | 0.091
100998 | 8.196 | 102.1 | 0.097
101093 | 8.291 | 101.9 | 0.095
total | 0.574 | 5.9288 | 0.09558333333
 | Total Impulse |  | 0.5666944667 | 5.553605773 | Ns
 | Specific Impulse |  | 123.4134616 | seconds
 | Average Thrust |  | 9.675271382 |  | Average Thrust is found by dividing the Total Impulse by the Thrust Time

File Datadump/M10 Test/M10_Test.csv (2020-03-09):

t | w
79140 | -18.2
79237 | -5.1
79333 | 2.3
79428 | 18.9
79524 | -10.3
79621 | -34.2
79717 | -32.7
79813 | -40.7
79909 | -38.2
80006 | -34.7
80102 | -29.5
80198 | -0.5
80294 | 33.1
80390 | 13
80486 | 10.2
80582 | 41.9
80678 | 95.7
80775 | 156.2
80871 | 197.1
80967 | 236.1
81063 | 370.8
81160 | 599.3
81256 | 469.7
81352 | 356.4
81448 | 324.4
81545 | 350.3
81641 | 382.7
81736 | 391.6
81832 | 368.9
81929 | 404.3
82025 | 419.1
82121 | 346.9
82217 | 252
82314 | 178.8
82410 | 123.7
82506 | 27.3
82603 | -22.9
82699 | -49
82795 | -69.4
82891 | -77.8
82987 | -78.6
83083 | -79.2
83179 | -73.2
83275 | -64.3
83372 | -71.4
83468 | -82.2
83564 | -78.9
83660 | -73.9
83757 | -71.8
83853 | -68.8
83949 | -62.7
84045 | -57.7
84142 | -60
84238 | -60.6
84334 | -57.8
84430 | -60.9
84526 | -59.3
84622 | -57.4
84718 | -59
84814 | -60.5
84911 | -63.1
85007 | -60.1
85103 | -51.7
85199 | -59.4
85296 | -60.8
85392 | -58.2
85488 | -61.4
85584 | -59.8
85681 | -56
85777 | -53.5
85873 | -61.7
85969 | -65.2
86066 | -58.6
86162 | -56.6
86258 | -58.5
86353 | -61.8
86450 | -64.7
86546 | -61.7
86642 | -57.5
86738 | -58
86835 | -61.2
86931 | -63.4
87027 | -58.5
87123 | -54.9
87220 | -61.6
87316 | -66.5
87412 | -70.2
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

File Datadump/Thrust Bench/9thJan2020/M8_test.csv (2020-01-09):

T | Time | Thrust
61706 | 0.193 | 5.3
61802 | 0.289 | 11.3
61898 | 0.385 | 21.4
61995 | 0.482 | 53.5
62091 | 0.578 | 139.5
62187 | 0.674 | 351.7
62283 | 0.77 | 654.1
62380 | 0.867 | 881
62476 | 0.963 | 1111.8
62572 | 1.059 | 1349.2
62668 | 1.155 | 1602.6
62765 | 1.252 | 1877.1
62861 | 1.348 | 2087.2
62957 | 1.444 | 2265.4
63053 | 1.54 | 2448.3
63150 | 1.637 | 2611.5
63246 | 1.733 | 2697
63342 | 1.829 | 2627
63438 | 1.925 | 2345
63535 | 2.022 | 1946
63631 | 2.118 | 1606.2
63727 | 2.214 | 1310.5
63823 | 2.31 | 1040.6
63920 | 2.407 | 804.4
64016 | 2.503 | 593.6
64112 | 2.599 | 416.9
64208 | 2.695 | 300.6
64305 | 2.792 | 227.2
64401 | 2.888 | 166.1
64497 | 2.984 | 115.4
64594 | 3.081 | 80.9
64690 | 3.177 | 55.2
64786 | 3.273 | 30.3
64883 | 3.37 | 7.2
64979 | 3.466 | 6
65076 | 3.563 | 5
65172 | 3.659 | 4.5
65268 | 3.755 | 0.5

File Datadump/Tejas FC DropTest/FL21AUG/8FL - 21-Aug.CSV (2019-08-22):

Time | Pascal | alt | KMF | ax | ay | az | Apo | Apo_KMF | v
35962 | 89613 | 518.25 | 515.92 | -32768 | 21104 | -5848 | 0 | 0
35992 | 89614 | 518.16 | 515.92 | 2400 | -12984 | -4336 | 0.09 | 0 | 0
36023 | 89614 | 518.16 | 515.93 | -7752 | -11848 | 4680 | 0 | -0.01 | 0
36052 | 89615 | 518.07 | 515.93 | 7044 | -10496 | -484 | 0.09 | 0 | 0
36083 | 89616 | 517.98 | 515.94 | 1632 | -18788 | 1116 | 0.09 | -0.01 | 0
36113 | 89617 | 517.88 | 515.95 | 1468 | -18336 | -3276 | 0.1 | -0.01 | 0
36144 | 89617 | 517.88 | 515.95 | 2436 | -15144 | -2248 | 0 | 0 | 0
36174 | 89618 | 517.79 | 515.96 | 3788 | -17436 | 1444 | 0.09 | -0.01 | 0
36204 | 89618 | 517.79 | 515.96 | 1880 | -20408 | -4656 | 0 | 0 | 0
36235 | 89619 | 517.7 | 515.97 | 1696 | -19972 | -3608 | 0.09 | -0.01 | 0
36264 | 89619 | 517.7 | 515.97 | 5996 | -22948 | -1856 | 0 | 0 | 0
36298 | 89619 | 517.7 | 515.98 | 2328 | -21072 | -1604 | 0 | -0.01 | 0
36329 | 89619 | 517.7 | 515.99 | 4236 | -18628 | -1804 | 0 | -0.01 | 0
36360 | 89620 | 517.6 | 515.99 | 3364 | -21200 | -1020 | 0.1 | 0 | 0
36390 | 89621 | 517.51 | 516 | 2924 | -26480 | -2480 | 0.09 | -0.01 | 0
36421 | 89621 | 517.51 | 516 | 2564 | -32768 | -6284 | 0 | 0 | 0
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

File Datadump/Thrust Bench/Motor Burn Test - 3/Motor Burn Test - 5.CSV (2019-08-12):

Time | time (s) | weight
92802 | 0 | 0.1
92806 | 0.004 | 0.3
92872 | 0.07 | 3.9
92968 | 0.166 | 9.2
93064 | 0.262 | 9.8
93159 | 0.357 | 9.7
93255 | 0.453 | 10
93350 | 0.548 | 9.8
93446 | 0.644 | 9.7
93542 | 0.74 | 9.8
93637 | 0.835 | 9.7
93732 | 0.93 | 9.8
93829 | 1.027 | 9.8
93924 | 1.122 | 9.8
94019 | 1.217 | 10.1
94115 | 1.313 | 10.1
94211 | 1.409 | 10.3
94306 | 1.504 | 10.3
94402 | 1.6 | 10.3
94497 | 1.695 | 10.4
94593 | 1.791 | 10.4
94689 | 1.887 | 10.4
94784 | 1.982 | 10.4
94879 | 2.077 | 10.5
94976 | 2.174 | 10.6
95071 | 2.269 | 10.6
95166 | 2.364 | 10.8
95262 | 2.46 | 10.9
95357 | 2.555 | 11
95453 | 2.651 | 11
95549 | 2.747 | 10.8
95644 | 2.842 | 10.9
95739 | 2.937 | 11
95836 | 3.034 | 11
95931 | 3.129 | 10.9
96026 | 3.224 | 10.7
96122 | 3.32 | 10.8
96218 | 3.416 | 11
96313 | 3.511 | 11
96409 | 3.607 | 10.8
96504 | 3.702 | 10.8
96601 | 3.799 | 10.8
96696 | 3.894 | 10.9
96798 | 3.996 | 10.9
96887 | 4.085 | 10.7
96983 | 4.181 | 10.6
97078 | 4.276 | 10.5
97174 | 4.372 | 10.4
97269 | 4.467 | 10.4
97364 | 4.562 | 10.5
97461 | 4.659 | 10.5
97556 | 4.754 | 10.6
97651 | 4.849 | 10.4
97747 | 4.945 | 10.3
97843 | 5.041 | 10.4
97938 | 5.136 | 10.2
98034 | 5.232 | 10.3
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

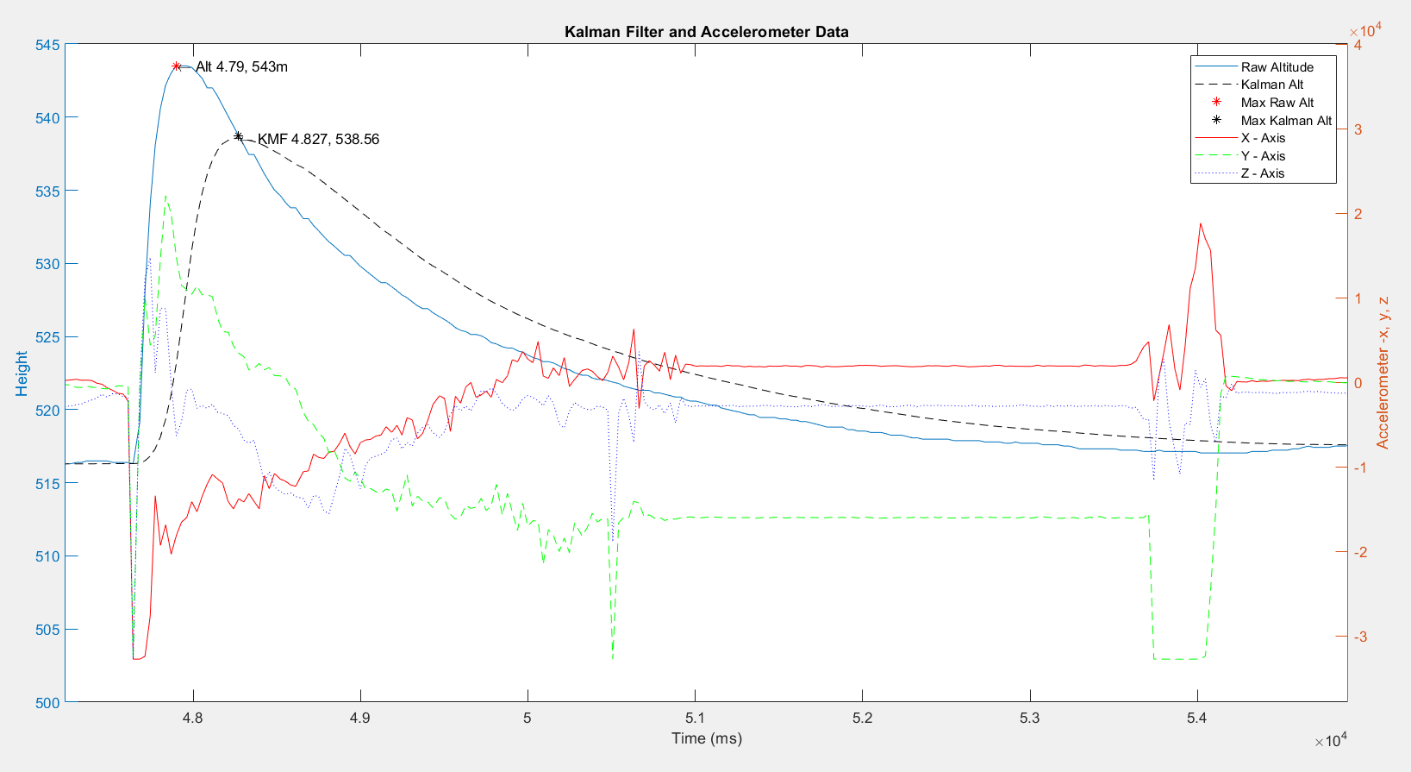
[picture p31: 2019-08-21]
Datadump/Tejas FC DropTest/FL21AUG/Annotation 2019-08-22 011342.png

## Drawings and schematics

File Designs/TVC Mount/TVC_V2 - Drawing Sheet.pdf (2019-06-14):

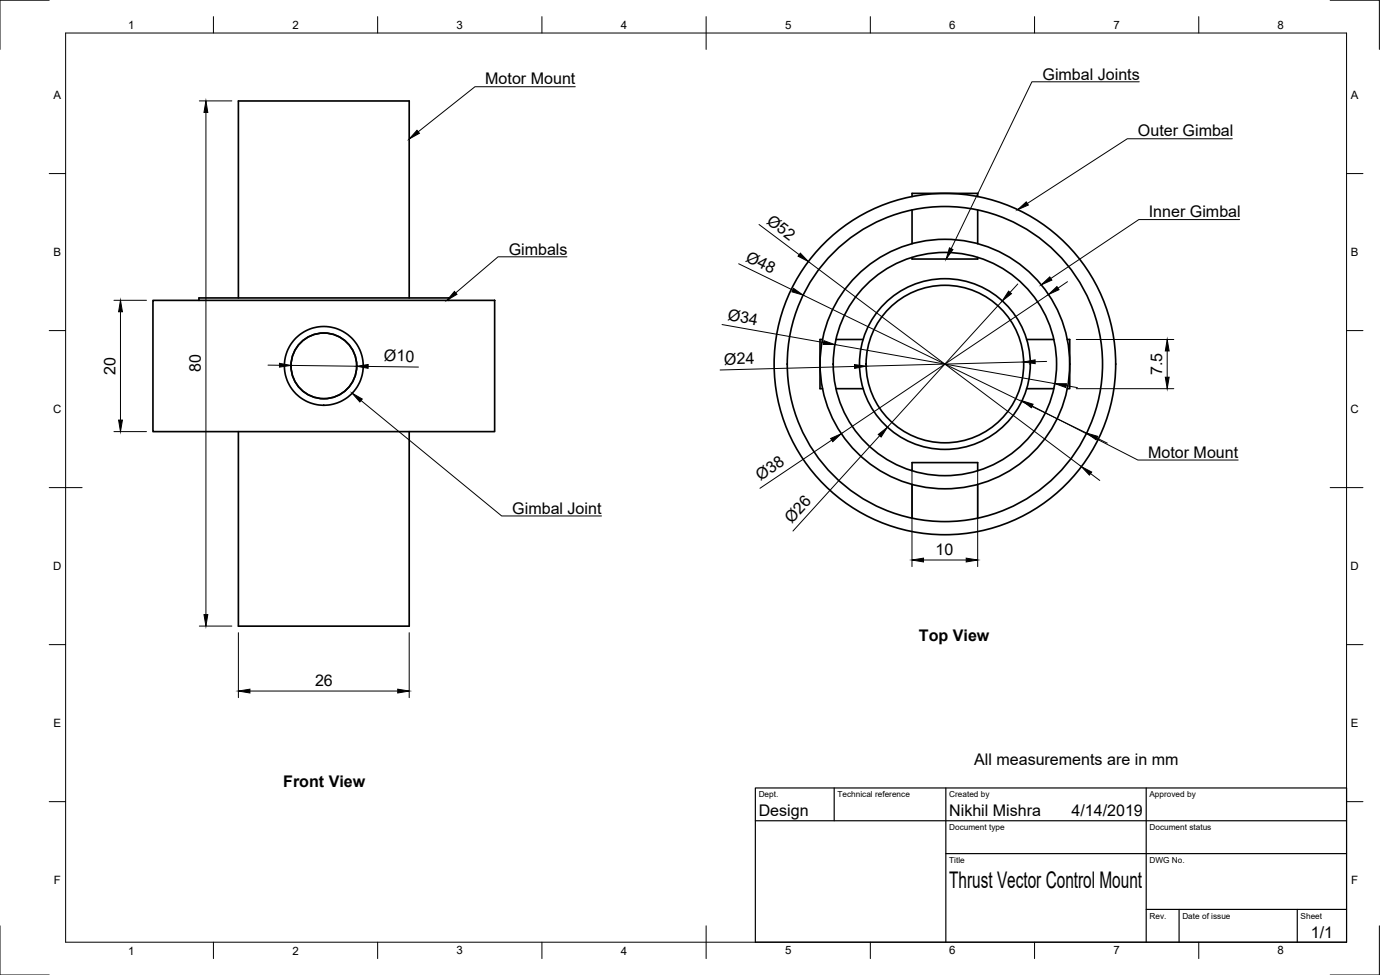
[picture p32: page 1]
Design; Nikhil Mishra 80; Outer Gimbal; Inner Gimbal; Motor Mount; Gimbal Joints; Gimbal Joint; Front View; Top View

All measurements are in mm

Dept. | Technical reference | Created by 4/14/2019 | Approved by

Document type | Document status

Title Thrust Vector Control Mount | DWG No.

Rev. | Date of issue | Sheet 1/1

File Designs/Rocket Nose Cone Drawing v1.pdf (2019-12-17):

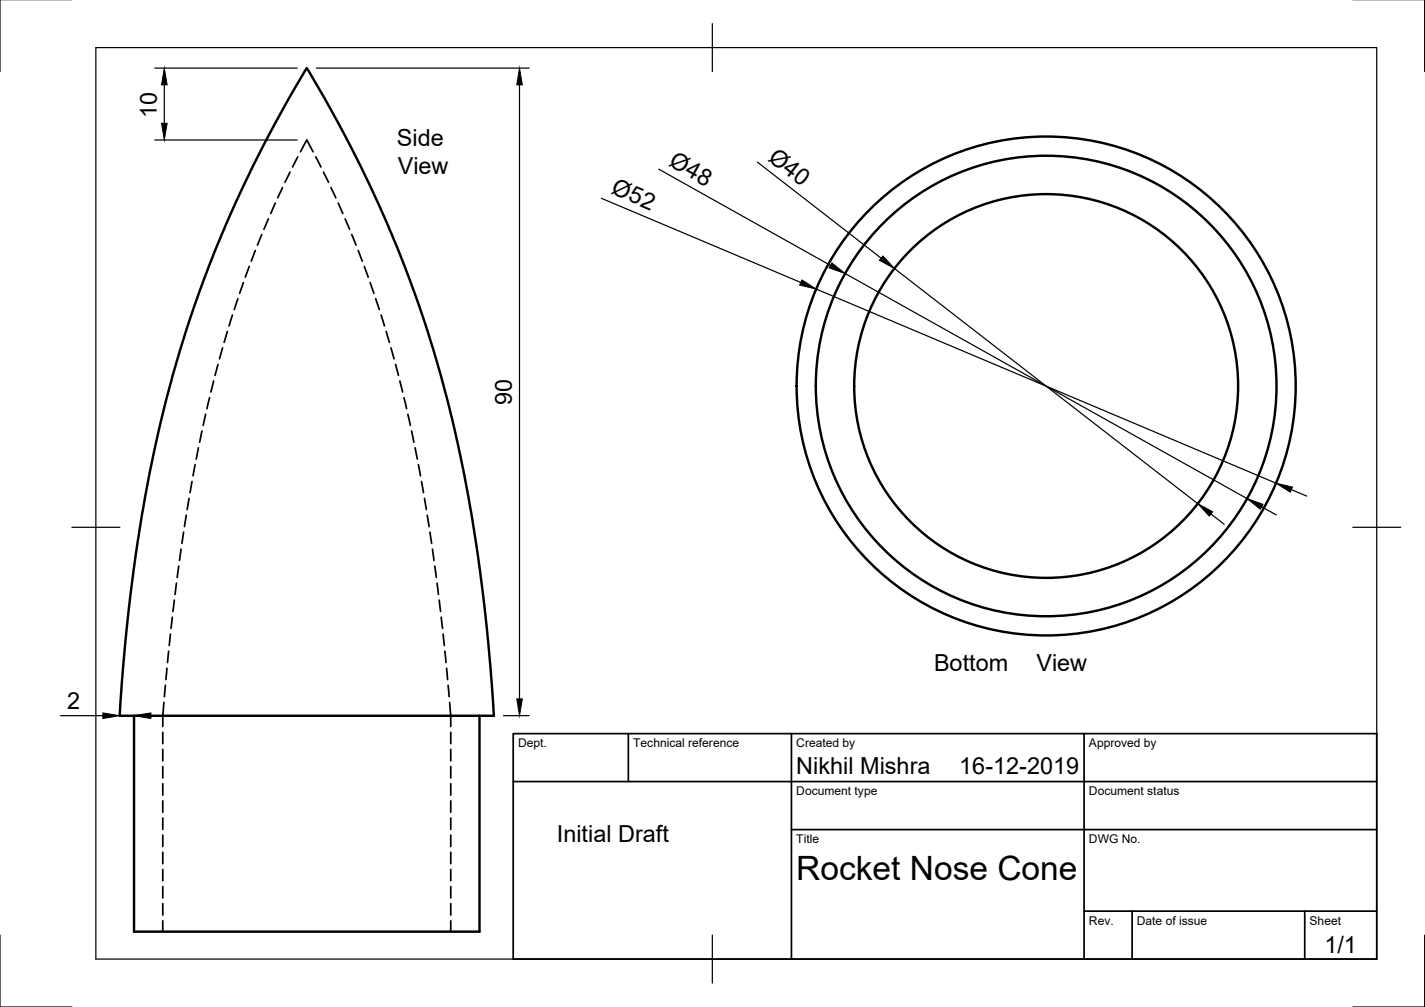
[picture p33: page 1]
Nikhil Mishra 90

Dept. | Technical reference | Created by 16-12-2019 | Approved by

Initial Draft | | Document type | Document status

Title Rocket Nose Cone | DWG No.

Rev. | Date of issue | Sheet 1/1

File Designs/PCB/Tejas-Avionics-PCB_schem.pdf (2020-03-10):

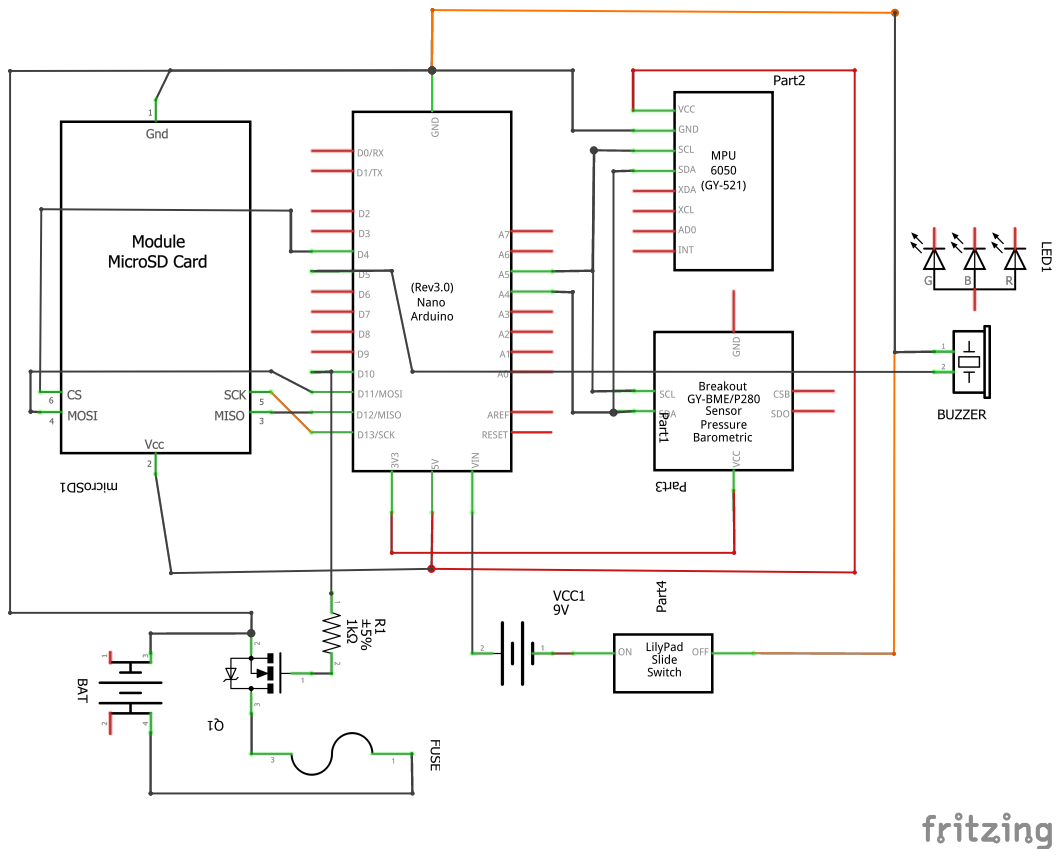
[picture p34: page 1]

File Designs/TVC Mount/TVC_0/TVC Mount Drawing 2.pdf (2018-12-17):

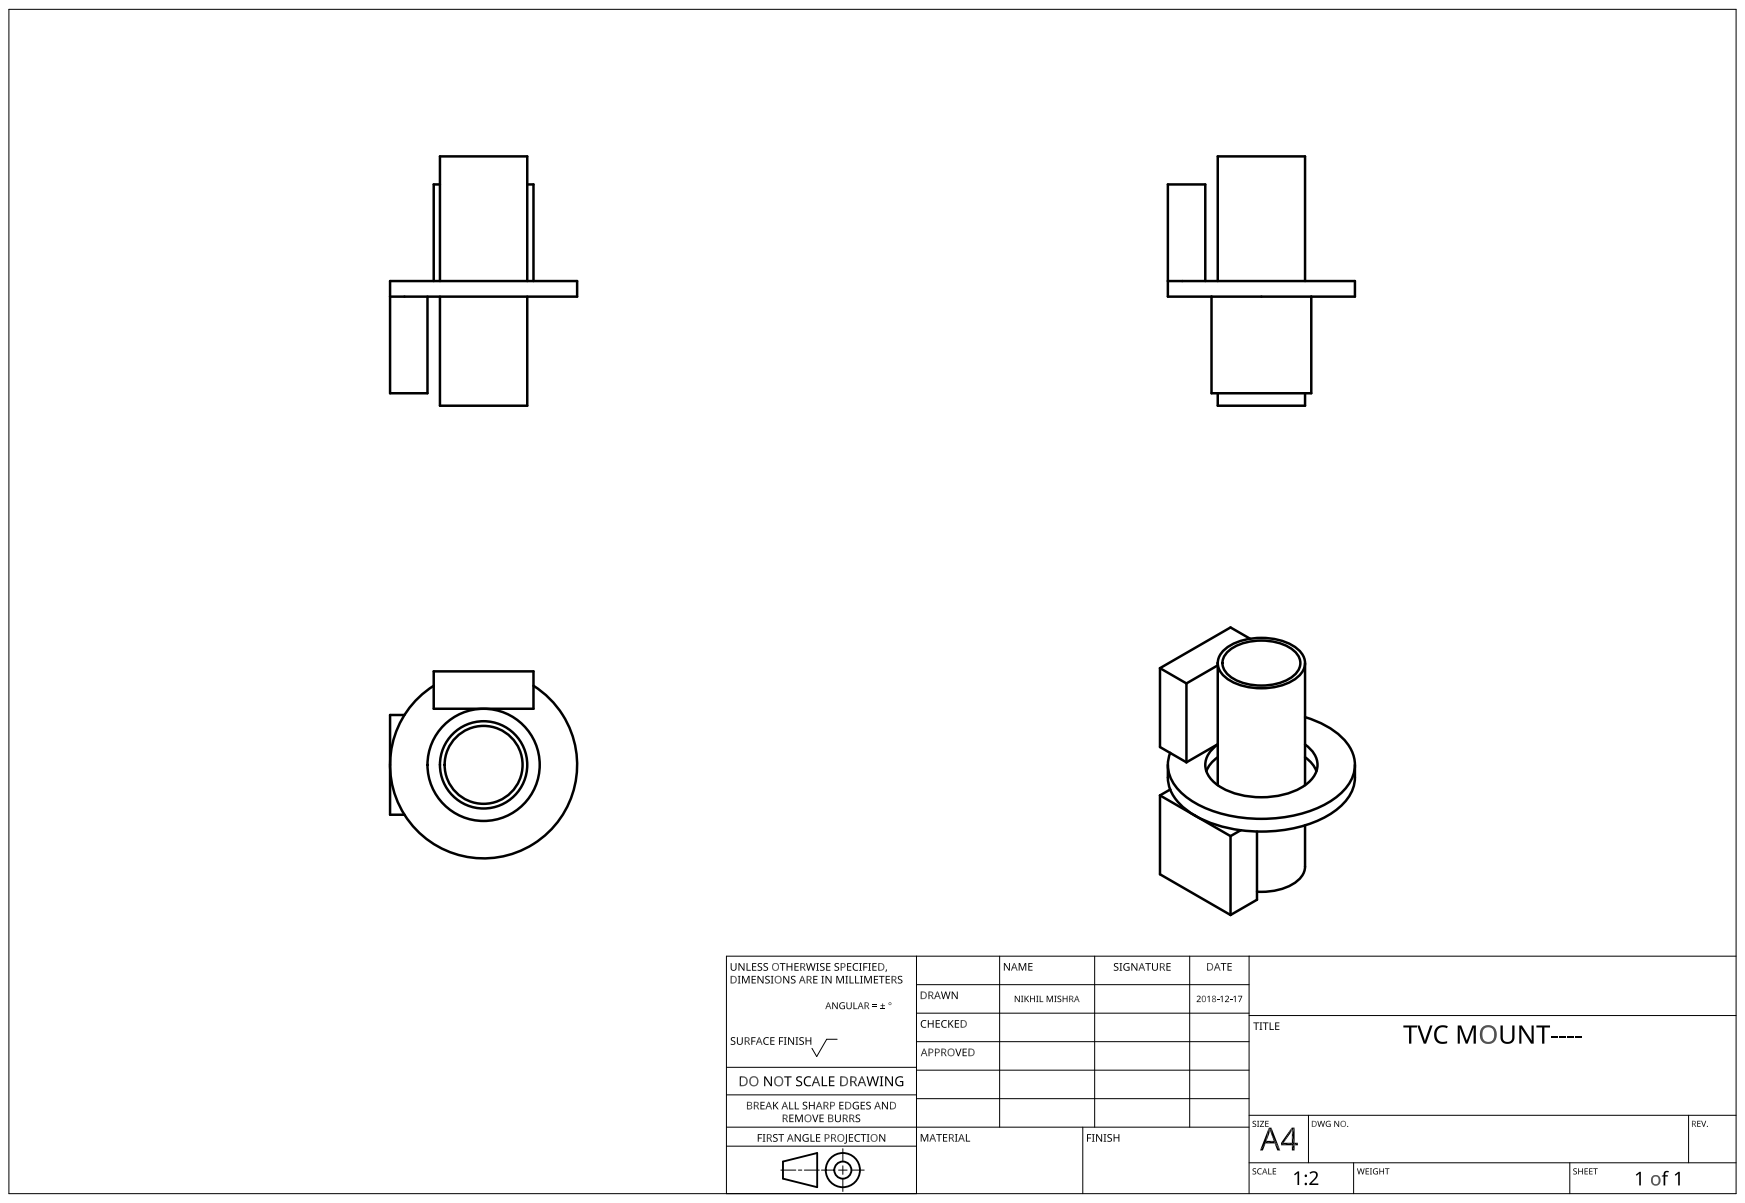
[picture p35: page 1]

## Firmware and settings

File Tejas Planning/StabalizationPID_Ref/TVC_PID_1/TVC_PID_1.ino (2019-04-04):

//https://github.com/bdureau/RocketMotorPIDGimbal

/*
   Description: Model Rocket motor gimbal using 2 servo. This is yet again another attempt to fly a model rocket without fins using long burn motors.
                It is using the Arduino PID controler to move a rocket motor.
                Angle changes can be monitored using a USB cable or a bluetooth interface
                Inspired by various camera gimbal projects
   Author: Boris du Reau
   Date: June 2018
   Sensor used is an MPU6050 board
   You can use an Arduino Uno/Nano or stm32F103C board
   Servo Connection
   BROWN - gnd
   red - 5v
   yellow - d10 (pwm for Sero X) or PA1 for stm32
          - d11 (servo Y) or PA2 for stm32
   MPU board Connection
   VCC - 5v
   GND - GND
   SCL - A5  or pin SCL on the stm32
   SDA - A4  or pin SDA on the stm32
   INT - D2 (not used)
  TODO:
  Build an Android interface to monitor the telemetry and configure it
*/


#include <Servo.h> //servo library
#include <I2Cdev.h>
#include <MPU6050_6Axis_MotionApps20.h> // Gyroscope and axcelerometer libraries
#include <PID_v1.h> // Arduino PID library
#include <Wire.h>

#define LED_PIN PC13 //pin 13 for the arduino Uno and PC13 for the stm32 
bool blinkState = true;

Servo ServoX;   // X axis Servo
Servo ServoY;   // Y axis Servo

float mpuPitch = 0;
float mpuRoll = 0;
float mpuYaw = 0;


// Create  MPU object
// class default I2C address is 0x68; specific I2C addresses may be passed as a parameter here
// for exemple MPU6050 mpu(0x69);
MPU6050 mpu;


// MPU control/status vars
uint8_t devStatus;      // return status after each device operation (0 = success, !0 = error)
uint16_t packetSize;    // expected DMP packet size (default is 42 bytes)
uint16_t fifoCount;     // count of all bytes currently in FIFO
uint8_t fifoBuffer[64]; // FIFO storage buffer

// orientation/motion vars
Quaternion q;           // [w, x, y, z]         quaternion container
VectorFloat gravity;    // [x, y, z]            gravity vector
float ypr[3];           // [yaw, pitch, roll]   yaw/pitch/roll container and gravity vector

// relative ypr[x] usage based on sensor orientation when mounted, e.g. ypr[PITCH]
#define PITCH   1     // defines the position within ypr[x] variable for PITCH; may vary due to sensor orientation when mounted
#define ROLL  2     // defines the position within ypr[x] variable for ROLL; may vary due to sensor orientation when mounted
#define YAW   0     // defines the position within ypr[x] variable for YAW; may vary due to sensor orientation when mounted

// PID stuff
//Define Variables we'll be connecting to
double SetpointX, InputX, OutputX;
double SetpointY, InputY, OutputY;

// Those initial tuning parameters need to be tuned
// this a bit like when you tune your copter appart from the fact that the rocket motor last only few seconds
// please help !!!!!!!
//double KpX = 2, KiX = 5, KdX = 1;
double KpX = 3.55, KiX = 0.005, KdX = 2.05;
//Specify the links and initial tuning parameters
//double KpY = 2, KiY = 5, KdY = 1;
double KpY = 3.55, KiY = 0.005, KdY = 2.05;
PID myPIDX(&InputX, &OutputX, &SetpointX, KpX, KiX, KdX, DIRECT);
PID myPIDY(&InputY, &OutputY, &SetpointY, KpY, KiY, KdY, DIRECT);


//calibration stuff
//Change those 3 variables if you want to fine tune the skecth to your needs.
int buffersize = 200;   //Amount of readings used to average, make it higher to get more precision but sketch will be slower  (default:1000)

int acel_deadzone = 8;   //Acelerometer error allowed, make it lower to get more precision, but sketch may not converge  (default:8)

int giro_deadzone = 1;   //Giro error allowed, make it lower to get more precision, but sketch may not converge  (default:1)

int16_t ax, ay, az, gx, gy, gz;

int mean_ax, mean_ay, mean_az, mean_gx, mean_gy, mean_gz, state = 0;
int ax_offset, ay_offset, az_offset, gx_offset, gy_offset, gz_offset;

/*
   Initial setup
   do the board calibration
   if you use the calibration function do not move the board until the calibration is complete
*/

void setup()
{

  ServoX.attach(PA1);  // attaches the X servo on PA1 for stm32 or D10 for the Arduino Uno
  ServoY.attach(PA2);  // attaches the Y servo on PA2 for stm32 or D11 for the Arduino Uno

  // set both servo's to 90 degree
  ServoX.write(90);
  ServoY.write(90);
  delay(500);

  Wire.begin();


  Serial1.begin(38400);
  while (!Serial1);      // wait for Leonardo enumeration, others continue immediately

  // initialize device
  Serial1.println(F("Initializing MPU 6050 device..."));
  mpu.initialize();

  // verify connection
  Serial1.println(F("Testing device connections..."));
  Serial1.println(mpu.testConnection() ? F("MPU6050 connection successful") : F("MPU6050 connection failed"));

  // load and configure the DMP
  Serial1.println(F("Initializing DMP"));
  devStatus = mpu.dmpInitialize();


  // INPUT CALIBRATED OFFSETS HERE; SPECIFIC FOR EACH UNIT AND EACH MOUNTING CONFIGURATION!!!!
  // use the calibrate function for yours
  // you can also write down your offset ans use them so that you do not have to re-run the calibration

  ax_offset = 1118;
  ay_offset = 513;
  az_offset = 1289;
  gx_offset = 64;
  gy_offset = -1;
  gz_offset = -33;
  // configure LED for output
  pinMode(LED_PIN, OUTPUT);
  calibrate();
  initialize();
}

void initialize() {
  // initialize device
  Serial1.println(F("Initializing MPU 6050 device..."));
  mpu.initialize();

  // verify connection
  Serial1.println(F("Testing device connections..."));
  Serial1.println(mpu.testConnection() ? F("MPU6050 connection successful") : F("MPU6050 connection failed"));

  // load and configure the DMP
  Serial1.println(F("Initializing DMP"));
  devStatus = mpu.dmpInitialize();
  mpu.setXAccelOffset(ax_offset);
  mpu.setYAccelOffset(ay_offset);
  mpu.setZAccelOffset(az_offset);
  mpu.setXGyroOffset(gx_offset);
  mpu.setYGyroOffset(gy_offset);
  mpu.setZGyroOffset(gz_offset);
  
  //turn the PID on
  //servo's can go from 60 degree's to 120 degree so set the angle correction to + - 30 degrees max
  myPIDX.SetOutputLimits(-30, 30);
  myPIDY.SetOutputLimits(-30, 30);
  myPIDX.SetMode(AUTOMATIC);
  myPIDY.SetMode(AUTOMATIC);
  SetpointX = 0;
  SetpointY = 0;
  // make sure it worked (returns 0 if so)
  if (devStatus == 0)
  {
    // turn on the DMP, now that it's ready
    Serial1.println(F("Enabling DMP"));
    mpu.setDMPEnabled(true);

    // get expected DMP packet size for later comparison
    packetSize = mpu.dmpGetFIFOPacketSize();
  }
  else
  {
    // ERROR!
    // 1 = initial memory load failed, 2 = DMP configuration updates failed (if it's going to break, usually the code will be 1)
    Serial1.print(F("DMP Initialization failed code = "));
    Serial1.println(devStatus);
  }
}


/*
   MAIN PROGRAM LOOP
*/
void loop(void)
{
  MainMenu();
  //myloop();
}

void myloop(void)
{
  // get current FIFO count
  fifoCount = mpu.getFIFOCount();

  // check for overflow (this should never happen unless our code is too inefficient)
  if ( fifoCount == 1024)
  {
    // reset so we can continue cleanly
    mpu.resetFIFO();
    Serial1.println(F("FIFO overflow!"));
    return;
  }

  // check for correct available data length
  if (fifoCount < packetSize)
    return;

  // read a packet from FIFO
  mpu.getFIFOBytes(fifoBuffer, packetSize);

  // track FIFO count here in case there is > 1 packet available
  fifoCount -= packetSize;

  // flush buffer to prevent overflow
  mpu.resetFIFO();

  // display Euler angles in degrees
  mpu.dmpGetQuaternion(&q, fifoBuffer);
  mpu.dmpGetGravity(&gravity, &q);
  mpu.dmpGetYawPitchRoll(ypr, &q, &gravity);
  mpuPitch = ypr[PITCH] * 180 / M_PI;
  mpuRoll = ypr[ROLL] * 180 / M_PI;
  mpuYaw  = ypr[YAW] * 180 / M_PI;

  // flush buffer to prevent overflow
  mpu.resetFIFO();

  // blink LED to indicate activity
  blinkState = !blinkState;
  digitalWrite(LED_PIN, blinkState);

  // flush buffer to prevent overflow
  mpu.resetFIFO();
  InputX = mpuPitch;
  myPIDX.Compute();
  InputY = mpuRoll;
  myPIDY.Compute();

  //if using PID do those
  ServoX.write(-OutputX + 90);
  ServoY.write(OutputY + 90);

  // if you do not want to use the PID
  // ServoX.write(-mpuPitch + 90);
  // ServoY.write(mpuRoll + 90);

  float q1[4];
  mpu.dmpGetQuaternion(&q, fifoBuffer);
  q1[0] = q.w;
  q1[1] = q.x;
  q1[2] = q.y;
  q1[3] = q.z;
  serialPrintFloatArr(q1, 4);
  Serial1.print(mpuPitch);
  Serial1.print("    ");
  Serial1.print(mpuRoll);
  Serial1.print("    ");
  Serial1.print(OutputX);
  Serial1.print("    ");
  Serial1.println(OutputY);
  delay(10);

  // flush buffer to prevent overflow
  mpu.resetFIFO();

}

// ================================================================
// === Those 2 functions will format the data                   ===
// ================================================================
void serialPrintFloatArr(float * arr, int length) {
  for (int i = 0; i < length; i++) {
    serialFloatPrint(arr[i]);
    Serial1.print(",");
  }
}


void serialFloatPrint(float f) {
  byte * b = (byte *) &f;
  for (int i = 0; i < 4; i++) {

    byte b1 = (b[i] >> 4) & 0x0f;
    byte b2 = (b[i] & 0x0f);

    char c1 = (b1 < 10) ? ('0' + b1) : 'A' + b1 - 10;
    char c2 = (b2 < 10) ? ('0' + b2) : 'A' + b2 - 10;

    Serial1.print(c1);
    Serial1.print(c2);
  }
}


/*
   calibration routines those will be executed each time the board is powered up.
   we might want to calibrate it for good on a flat table and save it to the microcontroler eeprom
*/
void calibrate() {
  // start message
  Serial1.println("\nMPU6050 Calibration Sketch");
  //delay(1000);
  Serial1.println("\nYour MPU6050 should be placed in horizontal position, with package letters facing up. \nDon't touch it until you see a finish message.\n");
  //delay(1000);
  // verify connection
  Serial1.println(mpu.testConnection() ? "MPU6050 connection successful" : "MPU6050 connection failed");
  //delay(1000);
  // reset offsets
  mpu.setXAccelOffset(0);
  mpu.setYAccelOffset(0);
  mpu.setZAccelOffset(0);
  mpu.setXGyroOffset(0);
  mpu.setYGyroOffset(0);
  mpu.setZGyroOffset(0);

  while (1) {
    if (state == 0) {
      Serial1.println("\nReading sensors for first time...");
      meansensors();
      state++;
      delay(100);
    }

    if (state == 1) {
      Serial1.println("\nCalculating offsets...");
      calibration();
      state++;
      delay(100);
    }

    if (state == 2) {
      meansensors();
      Serial1.println("\nFINISHED!");
      Serial1.print("\nSensor readings with offsets:\t");
      Serial1.print(mean_ax);
      Serial1.print("\t");
      Serial1.print(mean_ay);
      Serial1.print("\t");
      Serial1.print(mean_az);
      Serial1.print("\t");
      Serial1.print(mean_gx);
      Serial1.print("\t");
      Serial1.print(mean_gy);
      Serial1.print("\t");
      Serial1.println(mean_gz);
      Serial1.print("Your offsets:\t");
      Serial1.print(ax_offset);
      Serial1.print("\t");
      Serial1.print(ay_offset);
      Serial1.print("\t");
      Serial1.print(az_offset);
      Serial1.print("\t");
      Serial1.print(gx_offset);
      Serial1.print("\t");
      Serial1.print(gy_offset);
      Serial1.print("\t");
      Serial1.println(gz_offset);
      Serial1.println("\nData is printed as: acelX acelY acelZ giroX giroY giroZ");
      Serial1.println("Check that your sensor readings are close to 0 0 16384 0 0 0");
      Serial1.println("If calibration was succesful write down your offsets so you can set them in your projects using something similar to mpu.setXAccelOffset(youroffset)");
      //while (1);
      break;
    }
  }
}


void meansensors() {
  long i = 0, buff_ax = 0, buff_ay = 0, buff_az = 0, buff_gx = 0, buff_gy = 0, buff_gz = 0;

  while (i < (buffersize + 101)) {
    // read raw accel/gyro measurements from device
    mpu.getMotion6(&ax, &ay, &az, &gx, &gy, &gz);

    if (i > 100 && i <= (buffersize + 100)) { //First 100 measures are discarded
      buff_ax = buff_ax + ax;
      buff_ay = buff_ay + ay;
      buff_az = buff_az + az;
      buff_gx = buff_gx + gx;
      buff_gy = buff_gy + gy;
      buff_gz = buff_gz + gz;
    }
    if (i == (buffersize + 100)) {
      mean_ax = buff_ax / buffersize;
      mean_ay = buff_ay / buffersize;
      mean_az = buff_az / buffersize;
      mean_gx = buff_gx / buffersize;
      mean_gy = buff_gy / buffersize;
      mean_gz = buff_gz / buffersize;
    }
    i++;
    delay(2); //Needed so we don't get repeated measures
  }
}

void calibration() {
  ax_offset = -mean_ax / 8;
  ay_offset = -mean_ay / 8;
  az_offset = (16384 - mean_az) / 8;

  gx_offset = -mean_gx / 4;
  gy_offset = -mean_gy / 4;
  gz_offset = -mean_gz / 4;
  while (1) {
    int ready = 0;
    mpu.setXAccelOffset(ax_offset);
    mpu.setYAccelOffset(ay_offset);
    mpu.setZAccelOffset(az_offset);

    mpu.setXGyroOffset(gx_offset);
    mpu.setYGyroOffset(gy_offset);
    mpu.setZGyroOffset(gz_offset);

    meansensors();
    Serial1.println("...");
    blinkState = !blinkState;
    digitalWrite(LED_PIN, blinkState);
    if (abs(mean_ax) <= acel_deadzone) ready++;
    else ax_offset = ax_offset - mean_ax / acel_deadzone;

    if (abs(mean_ay) <= acel_deadzone) ready++;
    else ay_offset = ay_offset - mean_ay / acel_deadzone;

    if (abs(16384 - mean_az) <= acel_deadzone) ready++;
    else az_offset = az_offset + (16384 - mean_az) / acel_deadzone;

    if (abs(mean_gx) <= giro_deadzone) ready++;
    else gx_offset = gx_offset - mean_gx / (giro_deadzone + 1);

    if (abs(mean_gy) <= giro_deadzone) ready++;
    else gy_offset = gy_offset - mean_gy / (giro_deadzone + 1);

    if (abs(mean_gz) <= giro_deadzone) ready++;
    else gz_offset = gz_offset - mean_gz / (giro_deadzone + 1);

    if (ready == 6) break;
  }
}

//================================================================
// Main menu to interpret all the commands sent by the altimeter console
//================================================================
void MainMenu()
{
  char readVal = ' ';
  int i = 0;

  char commandbuffer[200];



  while (Serial1.available())
  {
    readVal = Serial1.read();
    if (readVal != ';' )
    {
      if (readVal != '\n')
        commandbuffer[i++] = readVal;
    }
    else
    {
      commandbuffer[i++] = '\0';
      break;
    }
  }

  if (commandbuffer[0] != '\0') {
    interpretCommandBuffer(commandbuffer);
    commandbuffer[0] = '\0';
  }
  myloop();
}

void interpretCommandBuffer(char *commandbuffer) {
  //Serial1.println((char*)commandbuffer);
  //this will erase all flight
  if (commandbuffer[0] == 'c')
  {
    Serial1.println(F("calibration\n"));
    // Do calibration suff
    state = 0;

    calibrate();
    mpu.setXAccelOffset(ax_offset);
    mpu.setYAccelOffset(ay_offset);
    mpu.setZAccelOffset(az_offset);
    mpu.setXGyroOffset(gx_offset);
    mpu.setYGyroOffset(gy_offset);
    mpu.setZGyroOffset(gz_offset);

  }
  else
  {
    Serial1.println(F("Unknown command" ));
    Serial1.println(commandbuffer[0]);
  }
}

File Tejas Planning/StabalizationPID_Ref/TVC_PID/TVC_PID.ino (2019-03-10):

//https://github.com/saustin123/active-stabilization/blob/master/MASTER_PROGRAM


#include <Wire.h>               //Including libraries
#include <Servo.h>
#include <Adafruit_Sensor.h>
#include <Adafruit_L3GD20.h>
#include <Adafruit_MMA8451.h>

#define RAD_DEG 57.295779 //Convert from radians to degrees
#define TAU 0.05          //Complementary Filter Time Constant
#define Kp 0.6            //PID constants
#define Ki 0
#define Kd 0.25

Adafruit_MMA8451 mma = Adafruit_MMA8451();

#define GYRO_CS 4 // labeled CS
#define GYRO_DO 5 // labeled SA0
#define GYRO_DI 6  // labeled SDA
#define GYRO_CLK 7 // labeled SCL
Adafruit_L3GD20 gyro(GYRO_CS, GYRO_DO, GYRO_DI, GYRO_CLK);

#define rollServo1_pin 9      //Sets Arduino pins for servos
#define pitchServo1_pin 11
#define calibrateLED_pin 2
#define launchReadyLED_pin 12
#define calibrateButton_pin 8
#define firstMotion_pin 13

Servo rollServo1;
Servo pitchServo1;

float rollAcc; //Accelerometer variables
float pitchAcc;
float zGravity;

float pitchGyro; //Gyro variables
float rollGyro;
float newTime;
float oldTime;
float pitchBias;
float rollBias;
boolean firstTime = 1;
float lastPitchRate;
float currentPitchRate;
float lastRollRate;
float currentRollRate;
float pitchRate;
float rollRate;
float dtSec;

float rollComplementary; //Complementary filter variables
float pitchComplementary;

float oldRollError; //PID variables
float rollErrorI;
float oldPitchError;
float pitchErrorI;
float oldTimePid;
float newTimePid;
boolean firstTimePid = 1;
float rollI;
float pitchI;
float rollPID;
float pitchPID;

boolean calibrate = 0;
boolean launchReady = 0;
boolean firstMotion = 0;

void setup() {
  Serial.begin(9600);      //Initializes IMU and microcontroller pins
  mma.begin();
  gyro.begin(gyro.L3DS20_RANGE_500DPS);
  mma.setRange(MMA8451_RANGE_8_G);

  pinMode(calibrateLED_pin, OUTPUT);
  pinMode(launchReadyLED_pin, OUTPUT);
  pinMode(calibrateButton_pin, INPUT);
  pinMode(firstMotion_pin, INPUT);

  digitalWrite(calibrateLED_pin, HIGH); //Calibrates the gyro and offsets the bias for each axis
  int N = 100;
  for (int i = 0; i < N; i++) {
    gyro.read();
    pitchBias += gyro.data.z;
    rollBias += gyro.data.y;
  }

  pitchBias /= (float) N;
  rollBias /= (float) N;
  
  rollServo1.attach(rollServo1_pin);
  pitchServo1.attach(pitchServo1_pin);

  rollServo1.write(90);       //Initializes and zeros the servos
  pitchServo1.write(90);
  digitalWrite(calibrateLED_pin, LOW);
}

void getGyroAngle() {
   if (firstTime) {     //Resets the time variables for the gyro if it is the first time through the loop
    oldTime = millis();
    newTime = millis();
    firstTime = 0;
    return;
  }
  gyro.read();          //Reads the gyro rate and the time since the function was last called
  newTime = millis();
  dtSec = ((newTime - oldTime) / 1000.0);

  currentPitchRate = (gyro.data.z - pitchBias); //Removes bias from each axis reading
  currentRollRate = (gyro.data.y  - rollBias);

  pitchRate = (lastPitchRate + currentPitchRate) / 2; //Takes an average of the readings to remove large spikes
  rollRate = (lastRollRate + currentRollRate) / 2;
 
  pitchGyro += (pitchRate * dtSec); //Calculates the angle by accumulating the rate of rotation over time
  rollGyro += (rollRate * dtSec);
  
  lastPitchRate = currentPitchRate; //Resets time variables
  lastRollRate = currentRollRate;
  oldTime = newTime;
}

void getAccAngle() {
  sensors_event_t event;  //Gets a new event from the accelerometer
  mma.getEvent(&event);
  
  float insideSqrt = 1-(event.acceleration.x * event.acceleration.x) - (event.acceleration.y * event.acceleration.y); //Removes the thrust vector from the accelerometer reading in order to isolate the gravity vector
  if(insideSqrt < 0) { //Removed negative values
    insideSqrt = 0;
  }
  
  zGravity = sqrt(insideSqrt); //Calculates the z component of gravity

  rollAcc = atan2(event.acceleration.y, zGravity) * RAD_DEG; //Calculates the angle using the arctangent function and the gravity vector values from the accelerometer
  pitchAcc =  atan2(event.acceleration.x, zGravity) * RAD_DEG;
}

void getComplementary() { //The Complementary Filter function obtains a more accurate angle reading by applying a low pass filter to the accelerometer and a high pass filter to the gyro
 getGyroAngle(); //Reads angles from gyro and accelerometer
 getAccAngle();
 
 float a = TAU / (TAU + dtSec); //calculates the filter coefficient a using the time constant and elapsed time

 rollComplementary = (a * rollGyro) + ((1-a) * pitchAcc); //Complementary Filter formulas
 pitchComplementary = (a * -pitchGyro) + ((1-a) * rollAcc);

 if(abs(rollComplementary) > 90) { //Resets filter values if the value exceed 90 - if the rocket arcs that far over, it is going to be almost impossible to correct
  rollComplementary = 0;
 }

 if(abs(pitchComplementary) > 90) {
  pitchComplementary = 0;
 }
}

void PID() {    //PID function
 float errorRoll; //Declares PID variables
 float errorPitch;
 float rollP;
 float rollD;
 float pitchP;
 float pitchD;
 float dPitchError;
 float dRollError;

 if (firstTimePid) {
    oldTimePid = millis(); //Resets time variables on the first loop
    newTimePid = millis();
    firstTimePid = 0;
    return;
  }
  getComplementary(); //Calls the complementary filter function and makes each reading the error for that axis (the setpoint is 0 degrees)
  newTimePid = millis();
  float dtSecPid = ((newTimePid - oldTimePid) / 1000.0);
  errorRoll = rollComplementary;
  errorPitch = pitchComplementary;

  rollP = Kp * errorRoll; //P value calculation
  pitchP = Kp * errorPitch;
  
  rollErrorI += (errorRoll * dtSecPid); //I value calculation
  pitchErrorI += (errorPitch * dtSecPid);
  rollI = Ki * rollErrorI;
  pitchI = Ki * pitchErrorI;
  
  dRollError = errorRoll - oldRollError; //D value calculation
  dPitchError = errorPitch - oldPitchError;
  rollD = Kd * dRollError;
  pitchD = Kd * dPitchError;

  rollPID = rollP + rollI + rollD; //Adds P, I, and D values for each axis
  pitchPID = pitchP + pitchI + pitchD;
  
  oldRollError = errorRoll; //Resets time variables
  oldPitchError = errorPitch;
  oldTimePid = newTimePid;

  if(rollPID > 90) { //Constrains PID values to [-90, 90]
  rollPID = 90;
 } else if(rollPID < -90) {
  rollPID = -90;
 }

if(pitchPID > 90) {
  pitchPID = 90;
 } else if(pitchPID < -90) {
  pitchPID = -90;
 }

  rollPID += 90;   //Maps output from [-90, 90] to [0, 180] required by servo
  pitchPID += 90;
}
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

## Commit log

2018-12-13 First Commit!
    CAD Designs!
    [Rocket Model.skp]
2018-12-14 Simple angle meter using ADXL335 accelerometer
    https://www.electronicsblog.net/simple-angle-meter-using-adxl335-accelerometer-arduino/
2018-12-17 Create TVC Mount Drawing 2.pdf
2018-12-18 i2c device not found
2018-12-20 Didn't work.
    Still not working #1
    [I2C_Scanner.ino]
2018-12-23 Fix #1 and Tests
    Fixed #1
    Tested servomotor
    have to understand that program! :+1:
    [I2C_Scanner.ino, MPU6050_Servomotor.ino, MPU_6050_Test.ino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]
2018-12-23 re organize
    [Rocket Model.skp]
2018-12-30 ReOrganised
    Tejas Alpha
    [Rocket Model.skp]
2018-12-30 servomotor control monitor
    test control of servo motor from serial monitor! :D
2018-12-31 added second servo
    fixed voltage problem!
    [ServoMotor_2.ino, ServoMotor_9g_SG90_Test.ino]
2019-03-04 sensor visualization kit
    AHRS Kit with processing 3
2019-04-04 imported files
    tejas is up!
    [Board Schematic V1.sch]
2019-07-01 added enables for Serial Prints
    [data_bmp.csv, flight_rawdata.csv]
2019-07-03 added PCB designs
    [Tejas-Avionics-PCB 5x7.fzz, Tejas-Avionics-PCB.fzz]
2019-07-28 Tejas Launchpad
    Rocket Motor Thrust Bench
    [CONFIG.txt, Tejas - Rocket Motor Test Bench.fzz]
2019-07-28 added a timer to launchpad test
2019-07-28 Tejas Thrust Test Bench Schematic
    [Tejas - Rocket Motor Test Bench.fzz]
2019-07-29 updated Thrust Bench
    now working properly.
    fix time lag
    [21TLP - Copy.csv, Tejas - Thrust Bench Data Viz.xlsx]
2019-07-29 changing dr
    updated folder structure for better understanding.
    [data_bmp.csv, flight_rawdata.csv]
2019-07-31 Launchpad Complete
    with Millis Fn.!!!!!!!!!
    YAY!!
2019-07-31 datadump update
    [21TLP - CSV.csv]
2019-08-02 fixed runtime bug
    just changed things around
    [BurnTest_Bench.ino]
2019-08-03 added Release Fire Button Alert.
    WARNING!
2019-08-07 loadcell pin
2019-08-07 thrust bench working properly!
    fixed silly bugs!
    [11TB.xlsx]
2019-08-12 bugs
    these bugs are dangerous!!!!!!!! VERY DANGEROUS!
    [BurnTest_Bench.ino]
2019-08-12 dr changes and buzzer for FC
    [CONFIG.txt]
2019-08-12 Create Motor Burn Test - 5.CSV
    [Motor Burn Test - 5.CSV]
2019-08-12 burn test 3 data
    [Motor Burn Test - 5.CSV]
2019-08-13 Tejas FC
    [CONFIG.txt]
2019-08-21 fixed dataoverflow bug!
    Yay!
    [i2c_BMP280.h, i2c_BMP280.ino]
2019-08-22 FL21AUG - Apogee Check Analysis
    [8FL - 21-Aug.CSV]
2019-08-23 FL21AUG - Amith
    [0FL.CSV, 10FL.CSV, 11FL.CSV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]
2019-08-23 update datadump
    [14FL.CSV, 16FL.CSV, 17FL.CSV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]
2019-09-14 parachute test
    [0FL.CSV, 1FL.CSV, 2FL.CSV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]
2019-09-16 bmp280 calibration bug
2019-09-16 Fixed alt bug and added new Ada Lib
    finally has calibration according to MSL!
    [CONFIG.txt]
2019-12-17 new CAD designs
    [BlastCoupler v2.stl, Coupler1 v3.stl, Coupler1 v4.stl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]
2019-12-17 Thermal Report for Coupler
2019-12-18 pcb tejas designs
    [TEJAS 2_PCB.fzz]
2019-12-18 Rocet motor mount
    [BlastCoupler v1.obj, BlastCoupler v2.stl, Coupler1 v4.obj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]
2019-12-18 final CAD files for print
    [MotorMount - Bolt V2.stl, MotorMount - Bolt.stl, MotorMount - Nut V2.stl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]
2019-12-25 new FC CAD designs.
    [FC_Lower_Mount_V6.stl, FC_Upper_Mount_V6.stl, MotorMount - Bolt V2.stl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]
2019-12-25 changed size of coupler
2019-12-30 flowchart for V2
2019-12-31 added final v of FC
    [FC_Upper_Mount_V8.stl]
2020-01-08 launchpad bugs
    [Calculation for Test.xlsx]
2020-01-09 thurst data 9th Jan
    [Calculation for Test.xlsx, M8_test.csv]
2020-01-09 New thrust data
2020-02-12 Apogee Test & Sims
    Feb 2020
    [0FL.CSV, 1FL.CSV, 5FL.CSV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]
2020-02-19 new data
    [Apo0FL.CSV]
2020-02-21 Pre Launch Changes
    BT_ABORT not working
    M1 not working
    [Launchpad_Computer.ino]
2020-02-22 Final Launch Bug Fixes
    pre launch fixes
    - fallr - 0.02
    - Pyro disables after landing only
    [Tejas_V2_FC.ino]
2020-03-09 TL2 launch files
    [1FL.CSV, 6FL.CSV, FC_Lower_Mount_V10.stl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]
2020-03-10 Added V4 Tejas FC
    Added:
    Pitch Abort Program
    The Led glows red when in Launch Phase
    File will close after 2 seconds, so that the KMF will get more readings
2020-03-10 pcb designs latest
    [Tejas-Avionics-PCB.fzz]
2020-04-12 deleted flowchart
2020-04-12 pitch program
